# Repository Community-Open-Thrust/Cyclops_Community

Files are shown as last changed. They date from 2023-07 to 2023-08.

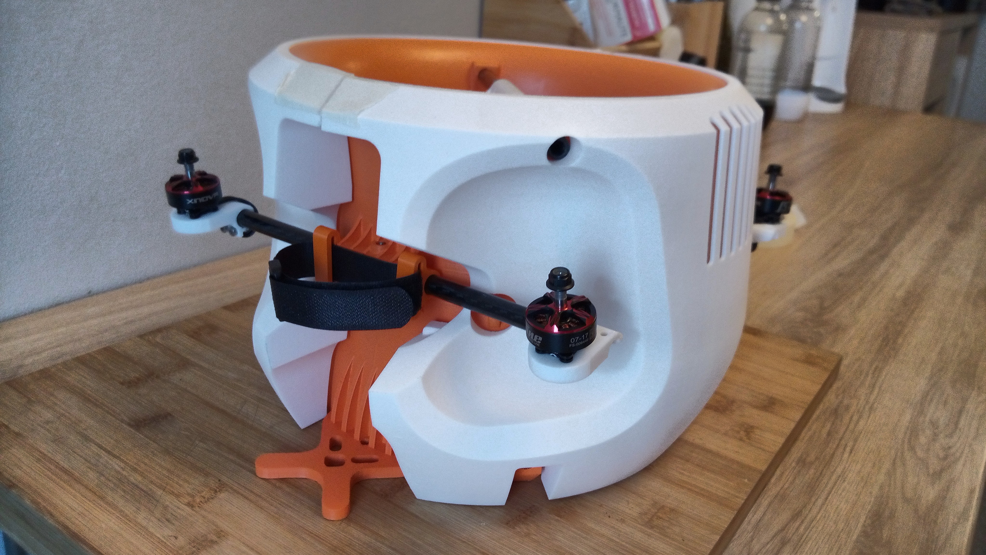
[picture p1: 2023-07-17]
Engineering/Photos-Assemblage-MarkII/IMG_20211008_180041_DRO.jpg

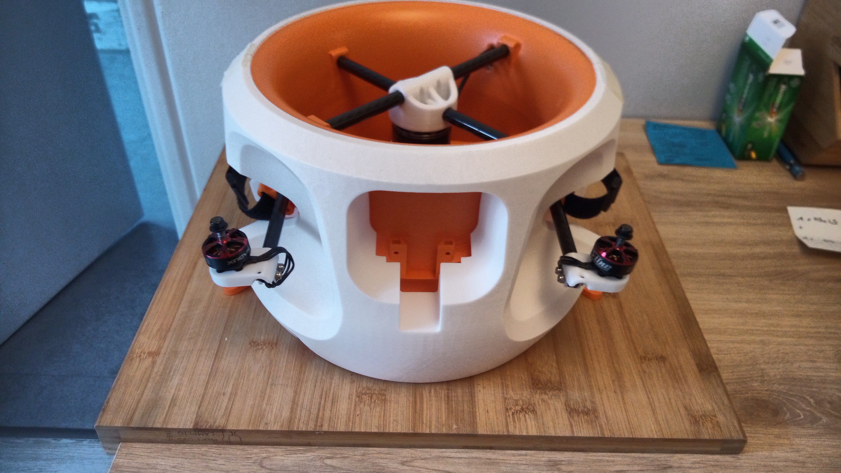
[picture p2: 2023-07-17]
Engineering/Photos-Assemblage-MarkII/IMG_20211008_180009_DRO.jpg

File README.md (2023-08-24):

# Cyclops / Cyclope Indoor Drone Community Edition

This is the repository for the Community Edition Release of the community of makers from Neva Aerospace Ltd (UK) for the turbo-drone Cyclope / Cyclops series for Indoor.

Cyclope v2 modifie - mise en situation interieur usine 2

Cyclops series are derived from Athena electric turbines / Electric Ducted Fans (EDF) 

# THE LICENCE IS CERN-OHL-S (Strongly Reciprocal) V2
https://ohwr.org/cern_ohl_s_v2.pdf


The LICENCE IS CERN Open Hardware Licence V2 "CERN-OHL-S V2" (Strongly Reciprocal). It applies to this repositrory and all Open-Thurst Community Repositories and contained sources.

Any further fork and/or modification must bear the following "Acknowledgement Notice" as per chapter 1.10 of Definition of the CERN-OHL-S V2 Licence:
"Acknowledgement of the Original Authors: Neva-Aero and the Human Team Members between 2016 and 2022 : F.M. Robert Vergnes, Valentin Bertrand, Kevin Pantoja, Olivier Chevillard, Elie de Fonclare, David Brotherton-Ratcliffe, Renaud-Pierre Blanpain, Anthony Gambus", and "Cyclops Series - Open-Thrust Community Edition - Licence CERN-OHL-S-V2", both Notice to be visible in the documentation with a link to the github Source.

And as per chapter 4 , the Visible Notice is "Cyclops Series - Open-Thrust Community Edition - Licence CERN-OSL-S-V2" and must be visible on the product.

# About using this repository
MAIN WILL NOT CHANGE.
The main of repository will be locked to the initial commit to avoid losing information. 
Please do create a new branch for a new version or create your own fork.
Please check the branch for the early or the last version of the project.

# Serialisation & History
The current Cyclops-K-Mark-II.2, it is an evolution of several design trials.
The first flight occured in May 2021 and then the prototyping went through several iterations.
The Cyclope-K-Mark-II has limitations and it requires more development to achieve its full potential.

# Warranties & Disclaimers

The Warranties and Disclaimers from the LICENCE IS CERN-OHL-S (Strongly Reciprocal) V2 apply to all Open-Thurst Community Repositories and contained sources.
https://ohwr.org/cern_ohl_s_v2.pdf

Extract:

6 DISCLAIMER AND LIABILITY 

6.1 DISCLAIMER OF WARRANTY – The Covered Source and any Products are provided ‘as is’ and any express or implied warranties, including, but not limited to, implied warranties of merchantability, of satisfactory quality, non-infringement of third party rights, and ﬁtness for a particular purpose or use are disclaimed in respect of any Source or Product to the maximum extent permitted by law. The Licensor makes no representation that any Source or Product does not or will not infringe any patent, copyright, trade secret or other proprietary right. The entire risk as to the use, quality, and performance of any Source or Product shall be with You and not the Licensor. This disclaimer of warranty is an essential part of this Licence and a condition for the grant of any rights granted under this Licence. 

6.2 EXCLUSION AND LIMITATION OF LIABILITY – The Licensor shall, to the maximum extent permitted by law, have no liability for direct, indirect, special, incidental, consequential, exemplary, punitive or other damages of any character including, without limitation, procurement of substitute goods or services, loss of use, data or proﬁts, or business interruption, however caused and on any theory of contract, warranty, tort (including negligence), product liability or otherwise, arising in any way in relation to the Covered Source, modiﬁed Covered Source and/or the Making or Conveyance of a Product, even if advised of the possibility of such damages, and You shall hold the Licensor(s) free and harmless from any liability, costs, damages, fees and expenses, including claims by third parties, in relation to such use. 

One last reminder, drones and/or turbines (electric ducted fans) can be dangerous if misused or made or used by non-trained technicians or engineers. You have been warned. All risks are yours.

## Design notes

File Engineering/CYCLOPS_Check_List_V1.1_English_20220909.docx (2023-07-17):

# CYCLOPS - TurboDrone

# PILOT CHECKLIST

# 1 PRE-FLIGHT

Purpose: To ensure that the aircraft is in flight order

## 1.1 Step 1: Central Turbine Inspection

• All the blades are present

• Rotors spin freely

• No major impact in the Shroud

## 1.2 Step 2: Inspection of auxiliaries

• All propellers are in good condition

• The motors do not rotate around the carbon axis

• The fairings are fixed and in good condition

## 1.3 Step 3: General Inspection

• No bare cables

• No free cables that could change when entering

• Landing feet are attached and in good condition

- Ensure that your HEREFLOW sensor is cable-connected and screwed to the drone
- Ensure that your Lidar sensor is cable-connected and screwed

# 2 PAYLOAD MOUNTING

Objective: Prepare the drone for an inspection mission

BEWARE THE DRONE CYCLOPS SERIES MUST HAVE A PAYLOAD TO FLY OR DEAD-WEIGHT MASS

## 2.1 Step 1: Choose your flight configuration

• Setup 1: Insta360 Camera

• Config 2: Feyiu Gimbal + Thermal Camera

• Config training: Add the fake camera (equivalent to Config1) with weight inside (orange fake camera)

## 2.2 Step 2: Mount the payload

• Mount the inspection elements on the front plate (camera, etc.)

• Mount balancing weights if needed

• Check balance - that the weights are correct for the chosen Config. – handle the drone by the top handle either by hand or through a carbon rod to check if there is any major disbalance.

Important: Make sure everything is secure and nothing can come loose in flight

# 3 GETTING STARTED

Objective: Prepare the drone for start-up

## 3.1 Step 1: Prepare the batteries

• Check the state of charge of the batteries

• Position the 2 batteries on the battery supports

• Fasten the batteries with the straps – make sure to lock the cables in the strap

• Mount low battery alarms on balancing sockets

• Make sure that no cables are close to the auxiliary motors

## 3.2 Step 2: Preparation of pilot equipment

• Switch on the Radio Control

• Turn on telemetry items

## 3.3 Step 3: Getting Started

• Connect the 2 batteries

• Check the connection between the drone and the RC (green led on the receiver and crossfire)

• Check the telemetry connection

• Check that the Pixhawk has initialized correctly (sound signal)

- Check that your RC respond on all modes: Stabilize, AltHold, Loitter – check on the telemetry screen
- Arm check: when armed on stabilize or althold ONLY the auxiliaries motors will start.

# 4 BEFORE THE FIRST TAKE OFF OF THE DAY

AFTER major transportation (airplane, trucks, or mishandling, or boat shipping) or several month unattended: Ground-run-up is mandatory

- Drone attached / strapped on a support of more than 5 KG – strap through the lower in-turbine carbon tube.
- Do not strap landing gears – strap on carbon tubes!
- Getting started & verification of use
- Power up in 10% increments for 10 seconds
- At each level check the noise (no abnormal vibration)
- Go to the next level +10% and thus up to 100% power

In the event of abnormal vibration at a bearing, stop the turbine and carry out the usual checks or suspend the activity.

• Once process is ended, cut the throttle. Do a quick visual inspection

• Add 5% throttle for 20-30s to cool motors of the EDF (central turbine).

# 5 LIFT-OFF

## 5.1 Step 1: Arm the drone

• Arm the drone (radio control)

Select mode: Stabilise or AltHOLD for take-off

It is advised not to take-off on Loitter indoor due to the nature of thr dround which may or may not be suitable for the Loitter sensor (Hereflow).

• Check that the 4 auxiliary motors are running well

• Very slightly increase throttle

• Check that the central turbine turns well

- In AltHold (and Loitter) take-off : the Central turbine ramps-up according to Pixhawk and it takes few seconds for Piwhaxk to ramps up the turbine – be gentle and patient.

## 5.2 Step 2: Put the drone in the air

• Gradually increase the throttle until the drone starts to lift (throttle approx. 50%) – be patient as turbine ramps for take-off is managed by Pixhawk.

• Give a small pulse on the throttle to put the drone in the air

• Stabilize the drone at eye level then start the mission

On K-001 & K002 drone on Stabilize and AltHold the drone needs a bit of pitch-forward as it tends to shift back – it is a known issue to be corrected. – Pixhawk does correct as soon as you switch to loiter mode.

## 5.3 Loiter mode:

When on Stabilize or AltHold and the drone is at +1M and stable:

- You can switch to Loiter,
- wait 2 seconds and move your drone gently around
- check if there is no “HERFLOW / XY error” – as this would indicate that the ground is not compatible with the ToF Herflow Senor sensor and you need to revert back to AltHold. If there is no error, you are free to loiter to your will.
- Fly Safe and respect regulations

# 6 LANDING

• Landing Modes: Stabilise, ALtHold, Loitter. All modes are fine for landing

The Landing gears can break on hard landing. Landing gears are wearables and are designed to break on hard landing to absorb the energy of a hard landing and keep the drone safe. You have spare landing gears and the landing gears can be changed easily with zip-tights.

- As soon as the pilot hears the battery alarm, he must IMMEDIATELY enter the landing phase
- You can set battery alarm on your RC or Telemetry (by default Alarm is set to Telemetry).

• Gradually reduce throttle to lose altitude

• A few centimetres from the ground (10-20cm), level off, then reduce the throttle again to land

Note: In this phase the drone is subject to ground effects corrected by Pixhawk on Loiter mode only. For Stabilize and AltHold pilot need to pay attention to landing phase.

• Once on the ground, cut the throttle. Do a quick visual inspection

• Add 5% throttle for 20-30s to cool motors for the central turbine. This is needed. Please avoid stopping the motor of the Cyclops abruptly. Abruptly stopping turbine motors creates a thermal discharge due to the high current within the motor and ESC.

Important: No battery failsafe is set - only the pilot is responsible for his battery level

Neva Aerospace / © - 2022 1 / 2

CYCLOPS CHECKLIST – Nr. 202209

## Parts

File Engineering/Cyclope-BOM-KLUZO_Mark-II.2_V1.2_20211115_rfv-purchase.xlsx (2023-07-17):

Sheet: Header
File: | Cyclope K BOM File
Version | 1.2
Date | 2021-01-19

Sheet: KLUZO_BOM_PROTO
Cyclope Kluzo BOM
Last Edited by |  |  | NEVA VB – 19/01/2021
0 – General Specifications
Reserved for Neva
MTOW (gr) |  | 3400
Available Payload (gr) |  | 631
Autonomy (min) |  | 11
1 – Ready-to-fly Kluzo (without inspection equipment)
Reserved for Neva
Item Name | Units | Makes | Details | Total Weight (gr)
I – Main Body
SHO | 2 | NEVA |  | 750
STA | 2 | NEVA
ROT | 2 | NEVA
BLA | 10 | NEVA
CAP | 2 | NEVA
AUX_SHO | 4 | NEVA |  | 100
AUX_STA | 2 | NEVA | Carbon tube + motor adapter | 20
AUX_BLA | 4 | HQPROP | HQ 3x4x3 V1S | 8
II – Electronics
MOT | 2 | TMOTOR |  | 275
ESC | 2 | CASTLE |  | 40
AUX_MOT | 4 | TMOTOR | TMOTOR F1507 kv2700 | 60
AUX_ESC | 1 | TMOTOR | ESC Tmotor 4in1 V45A 6s 32 BIT | 20
III – Flight Control
PIX_MINI 4 | 1 | HOLYBRO |  | 16
SONARS | 3 | MAXBOTIXS |  | 25
RC_CONTOL | 1 | TBS | 868 MHz crossfire RX (https://www.studiosport.fr/recepteur-tbs-crossfire-nano-rx-se-a16057.html) | 5
TELEM | 1 | TBD | 433MHz telemetry | 30
IV – Power System
BAT | 2 | SLS | For 11min Flight : SLS4500mAh 6S 30/60C | 1300
BEC | 1 | CASTLE | Castle 6S – 5v – 10a (1xfor Pixhawk, 1xfor Accessories) | 15
HARNESS | 1 | NEVA | Power harness : 16awg+ xt90 connectors | 80
PWR_MODULE | 1 | TBD | Power module for pixhawk | 25
 |  |  | Total RTF weight (gr) | 2769
2 – Inspection Equipment
To be completed by Pilgrim
Item Name | Units | Makes | Details (please provide internet links) | Total Weight (gr) | Remaining Payload (gr)
Equipement de Base
Led lights | 4 | E44 electronique | 1W led light cold white(6000K) 3-3,6V (1Gr/led) http://www.e44.com/composants/composants-actifs/optoelectronique/led/leds-cms/led-haute-puissance-1w-blanc-froid-LED1WCMS-BLANC.html | 4 | 558.2 | ATTENTION : Température max : 125°C – Polycarbonate en impression obligatoire – Mettre les radiateurs dans le flux des moteurs aux
Heat dissipator led lights | 4 | RS component | https://fr.rs-online.com/web/p/dissipateurs-de-chaleur/7226827/?matchtype=&pla-303373399821&gclsrc=aw.ds | 40
FPV camera | 1 | Foxeer | 1 foxeer t-rex micro 1500tvl camera used for navigation https://www.foxeer.com/foxeer-t-rex-micro-1500tvl-6ms-latency-super-wdr-fpv-camera-g-308 | 8.6
FPV transmitter | 1 | TBS | Pro32Hv 25-1000mW 5,8Ghz https://www.studiosport.fr/emetteur-video-unify-pro32-hv-mmcx-team-black-sheep/ | 8.7
FPV Antenna | 1 | Foxeer | Foxeer pagoda Pro RPSMA RHCP | 11.5
Config 1 : camera 360°
SUPPORT CAMERA | 1 | Neva | NEW CAP INLET avec support camera | 50 | 378.2
360° camera | 1 | Insta360 | Camera Insta ONE R | 130 |  | DIMENSIONS : long 72 x hauteur 48 x profondeur 43
Config 2 : camera thermique
Gimbal/Stabilisateur Feiyu WG2 | 1 | FEIYUTECH | https://www.feiyu-tech.com/wg2/ | 238 | 210.2
FLIR Vue Pro | 1 | FLIR | https://www.flir.fr/products/vue-pro/ | 110

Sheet: Purchase_Parts-Suppliers
 | Item | Unit for 1 drone | Link 1 (FR) | Price total (€) unitaire | Prix Total | Link 2 (China) | Price (€) | Link 3 (USA) | Price (€)
Semaine 1 | Pixhawk Mini 4 Holybro | 1 | https://www.studiosport.fr/controleur-pixhawk-4-mini-holybro-a16951.html | 179.00 € | 179.00 €
 | Carrier Board Pixhak | 1 | https://www.airbot-systems.com/produit/mini-carrier-board-pdb-combo-pixhawk-cube/?lang=en | 100.00 € | 100.00 € | https://hexadrone.fr/cube-carrier-board/1753-mini-carrier-board-pour-pixhawk-2-hex-0094393522485.html
 | Pixhawk 2.1 | 1 | https://www.airbot-systems.com/produit/cube-orange-pixhawk2-1/?lang=en | 250.00 € | 250.00 € | https://www.robotshop.com/eu/en/cubepilot-the-cube-orange-standard-set-ads-b-carrier-board.html
 | HQ 3x4x3 lot de 4 | 3 pack of 4 | https://www.banggood.com/fr/HQProp-DP3X4X3-3-blade-3Inch-Poly-Carbonate-POPO-Propeller-2CW+2CCW-p-1530875.html?ID=6157193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 |  |  | https://fr.banggood.com/HQProp-DP3X4X3-3-blade-3Inch-Poly-Carbonate-POPO-Propeller-2CW+2CCW-p-1530875.html?ID=6157216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 | 9.00 € | BAD SERIES BURNING
 | T-motor f1507 kv 2700 | 4 | https://www.drone-fpv-racer.com/t-motor-f1507-2700kv-5494.html | 19.00 € | 76.00 € | https://fr.banggood.com/T-Motor-F1507-1507-2700KV-3-6S-or-3800KV-3-4S-Brushless-Motor-for-Cinewhoop-RC-Drone-FPV-Racing-p-1582951.html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 | 66.00 € | BAD SERIES BURNING
 | MOTEURS X-NOVA SMOOTH LINE 2207 - 1700KV | 4 | Moteur : https://www.drone-fpv-racer.com/moteurs-x-nova-smooth-line-2207-boite-de-4-4739.html | 22.00 € | 88.00 € |  |  | Martk-II.2
 | GEMFAN 4032 WINDANCER - 4PCS | 4 | https://www.drone-fpv-racer.com/gemfan-4032-windancer-4pcs-4886.html#/1137-couleur-clear_red | 3.00 € | 12.00 € |  |  | Mark-II.2
 | XT90 anti-spark | 3 | https://www.amazon.fr/Lead-Tech-Anti-%C3%89tincelle-Connecteur-Adaptateur/dp/B07D6QH421 | 4.00 € | 12.00 € | https://fr.banggood.com/Amass-Anti-Spark-Sparkproof-Connector-Plug-XT90-S-For-Batttery-p-946409.html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 | 7.00 €
 | Bullet banana connector 3,5mm | 1 | pack | 6.00 € | 6.00 € | https://fr.banggood.com/20-Pairs-3_5mm-Gold-Bullet-Banana-Connector-Plug-Male-and-Female-For-ESC-Battery-Motor-p-934281.html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 | 6.00 €
 | T-Motor MN4010 KV475 | 2 | https://www.aerolab.de/brushless-motoren/t-motor-mn-serie/t-motor-mn4010-kv475_100012_1011 | 71.00 € | 142.00 € | https://store-en.tmotor.com/goods.php?id=342
Semaine 2 | ESC YGE 35LVT | 2 | http://www.helidigital.com/shop/controleurs-/3958-yge-35-lvt.html | 120.00 € | 240.00 € | https://www.hoelleinshop.com/e-vendo.php?shop=hoellein&SessionId=&a=search&SearchStr=YGE+35LVT
 | BEC 6S Matek | 1 | https://www.drone-fpv-racer.com/matek-micro-bec-630v-5v9v-6646.html?search_query=bec&results=175 | 7.90 € | 7.90 €
 | TMOTOR ESC 4in1 45A VELOX V2 | 1 | https://www.drone-fpv-racer.com/t-motor-velox-v45a-v2-4in1-esc-6235.html | 41.90 € | 41.90 €
 | Radio Taranis X9 Lite | 1 | https://www.studiosport.fr/radio-taranis-x9-lite-a18054.html | 107.00 € | 107.00 €
 | 18650 Accu | 2 | https://www.studiosport.fr/batterie-18650-3000mah-sony-a19219.html | 13.00 € | 26.00 €
 | External Baro - Adafruit BMP280 | 1 | https://www.gotronic.fr/art-capteur-de-t-et-de-pression-ada2651-23891.htm | 15.00 € | 15.00 €
 | KIT Crossfire TBS | 1 pack only (do not multiply by the number pf drones) | https://www.drone-fpv-racer.com/tbs-crossfire-micro-tx-v2-starter-set-3585.html | 139.90 € | 139.90 € | https://www.studiosport.fr/crossfire-nano-tx-starter-set-tbs-a20613.html |  | https://www.drone-fpv-racer.com/tbs-crossfire-nano-tx-6687.html
 |  |  |  |  |  | *
Semaine 3 | Camera 360 – Insta One R Twin edition | 1 | https://www.studiosport.fr/insta360-one-r-twin-edition-a19552.html | 509.00 € | 509.00 €
 | Telem 433 | 1 | https://www.studiosport.fr/kit-de-telemetrie-mini-433mhz-100mw-3drobotics-a19366.html | 29.9 | 29.9 | https://www.studiosport.fr/kit-telemetrie-fpv-radio-433mhz-v3-a16473.html | En attente confirmation Valentin
 | FPV Transmitter | 1 | https://www.studiosport.fr/emetteur-video-unify-pro32-hv-mmcx-team-black-sheep/ | 49.9 | 49.9 | https://www.fpv-fly.fr/tbs-unify-pro32-hv-mmcx.html
 | Antenna | 1 | https://www.studiosport.fr/antenne-singularity-5-8-sma-coudee-a-90-long-rhcp-truerc-a19037.html | 21.9 | 21.9
Semaine 4 | Lipo SLS 6S 4500mAh | 2 | https://www.stefansliposhop.de/en/batteries/sls-quantum/sls-quantum-30c/sls-quantum-4500mah-6s1p-22-2v-30c-60c::1684.html | 86.00 € | 172.00 € | https://www.stefansliposhop.de/en/information-for-retailers-business-consumers:_:1030.html
 | Lidat Lite Down range | 1 | https://www.robotshop.com/eu/fr/capteur-distance-laser-lidar-lite-3.html | 130.00 € | 130.00 €
 | Sonar maxbotix EZ4 I2C -MB1242 | 3 | https://www.robotshop.com/eu/fr/sonar-performance-i2cxl-maxsonar-ez4-maxbotix.html | 40.00 € | 120.00 €
 | Sonar maxBotix EZ0 | 3 | https://www.robotshop.com/eu/fr/capteur-ultrason-ez0-maxbotix.html | 27.00 € | 81.00 € | Note : 1 facing front (to protect camera) + 1 facing back (to protect eectronics) + 1 facing down (for smooth landing) |  | https://www.gotronic.fr/art-lv-maxsonar-ez0-11547.htm
 | LED éclairage (300Lumen) | 4 | https://www.amazon.fr/gp/product/B08QCLL21S/ref=ppx_yo_dt_b_search_asin_image?ie=UTF8&th=1 | 3 | 12 |  |  | https://www.e44.com/composants/composants-actifs/optoelectronique/led/leds-cms/led-haute-puissance-3w-blanc-froid-LED3WCMS-BLANC.html
 | LED Beamo (alternate) |  | https://www.amazon.fr/dp/B0849ZP618/ref=cm_sw_r_wa_apa_glt_i_KY1DYVP49E1CYM1X9PAC?th=1 | 70
 | Radiator for LED
 | Gimbal | 1 | https://www.amazon.fr/Feiyu-Tech-Stabilisateur-motoris%C3%A9-Smartphone-Action/dp/B071L93YDV | 245.9 | 245.9
 | Tubes carbones | 2 | https://www.carbonetube.net/produit.php?cat=TCUB | 13 | 26 | Tube carbone 10x7x1000mm DRAPAGE (REF0132CTPP1070-1)
 | SD Card V60 or SanDisk Pro | 1 | https://www.amazon.fr/dp/B0713QB6PB?psc=1&smid=A1X6FK5RDHNB96&ref_=chk_typ_imgToDp | 60 | 60 | Sandisk Pro extrem
 | RpiZero WH | 1 | https://www.kubii.fr/cartes-raspberry-pi/2076-raspberry-pi-zero-wh-kubii-3272496009394.html | 15 | 15 | https://www.amazon.fr/gp/product/B07C7FHJDX/ref=ppx_yo_dt_b_asin_image_o04_s00?ie=UTF8&psc=1
 | Battery Buzzer | 1 | https://www.amazon.fr/gp/product/B07Q9JQ2ZZ/ref=ppx_yo_dt_b_asin_title_o01_s00?ie=UTF8&psc=1 | 13 | 13
 | I2C Hub 6 | 2 | https://www.gotronic.fr/art-hub-6-ports-i2c-grove-103020272-31348.htm | 2 | 4
 | I2C Hib x8 | 1 | https://www.amazon.fr/gp/product/B08CXWVSMC/ref=ppx_yo_dt_b_asin_title_o00_s00?ie=UTF8&psc=1 | 11 | 11
 | Grive Cable Y | 1 | https://www.gotronic.fr/art-5-cables-grove-en-y-110990092-30772.htm | 5 | 5
 | I2C Hib x4 PXWH | 1 | https://www.amazon.fr/gp/product/B08212X27Q/ref=ppx_yo_dt_b_asin_title_o01_s00?ie=UTF8&psc=1 | 9 | 9
 | I2C HAT - SparkFun Qwiic HAT | 1 | https://www.amazon.fr/gp/product/B07JBK2LBZ/ref=sw_img_1?smid=&psc=1 | 12 | 12 | https://www.sparkfun.com/products/14459
 | RTK Module I2C male | 1 | https://www.amazon.fr/dp/B076GP5B94?psc=1&smid=A1X7QLRQH87QA3&ref_=chk_typ_imgToDp | 5 | 5 | DS3231
 | Radiator RpiZerp | 1 | https://www.amazon.fr/Aluminium-Dissipateur-Radiateur-Raspberry-Pi%C3%A8ces/dp/B01LXWK626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 | 3 | 3
 | RTK Module - Female | 1 | https://www.amazon.fr/gp/product/B07MB8YGCR/ref=ppx_yo_dt_b_asin_title_o01_s00?ie=UTF8&psc=1 | 18 | 18 | DS3231 // R&D only | TBC
 | Thoman manhole case | 1 | https://www.thomann.de/fr/hardcase_hn16b_bass_drum_case.htm | 150 | 150
 | Mousse Ptédécoupée | 5 | https://www.vexi.fr/details/valises-plastique/mousses-valises/mousse-predecoupee-620mm/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 | 30 | 150 | https://www.amazon.fr/HMF-pr%C3%A9d%C3%A9coup%C3%A9e-Personnalisable-Mallette-Tabletop/dp/B07GTP3S97
 | Mousse Laser découpe JPJ | 1 | https://www.jpj-mousse.fr/ | 500 | 500
 | Carénages Extérieur | 2 | Sculpteo | 380 | 760
 | Shroud Intérieur | 1 | pm@freelabster.com | 700 | 700 | info@invent3d.design
 | Vernis
 | Bande Reflec | 1 | https://www.amazon.fr/gp/product/B0814VMWV6/ref=ppx_yo_dt_b_asin_title_o00_s00?ie=UTF8&psc=1 | 11 | 11
 | Autocollant Reflec | 1 | https://www.amazon.fr/gp/product/B00EXQQFEW/ref=ppx_yo_dt_b_asin_title_o00_s00?ie=UTF8&psc=1 | 6 | 6
 | 41

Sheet: ShortSpecs
Short Parts List
Item | Unit for 1 drone
Controlller & Power:
Carrier Board Pixhak | 1
Pixhawk 2.1 | 1
MOTEURS X-NOVA SMOOTH LINE 2207 - 1700KV | 4
GEMFAN 4032 WINDANCER | 4
ESC Auxiliaire - F35 - Heli T-MOTOR | 4
EDG Athena: (Central Booster)
T-Motor MN4010 KV475 | 2
Lipo SLS 6S 4500mAh | 2
Radio:
Radio Taranis X9 Lite | 1
KIT Crossfire TBS | 1
Telem 433 | 1
FPV Transmitter | 1
Antenna | 1
ASMV Module:
Sonar maxbotix EZ4 I2C | 3
RpiZero WH | 1
I2C HAT - SparkFun Qwiic HAT | 1
RTC Module I2C male | 1

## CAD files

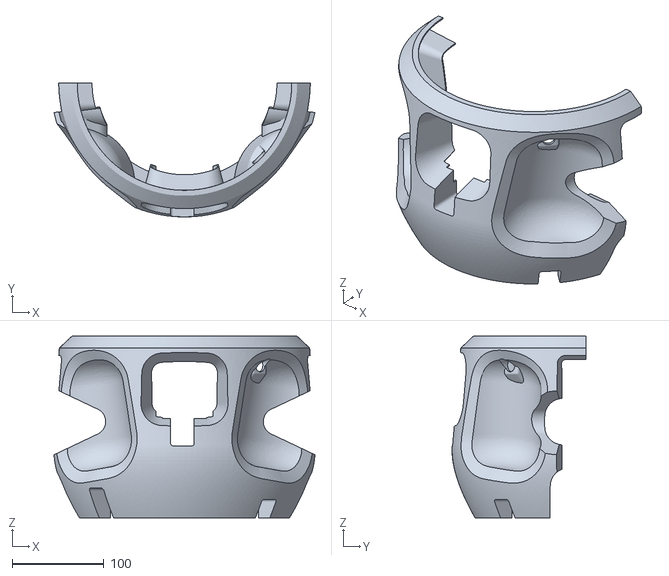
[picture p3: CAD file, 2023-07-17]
Engineering/CAD_3D/Covers_Capotages/Front-carenage-cyclope-mkII.stl
285.0 x 146.2 x 198.5

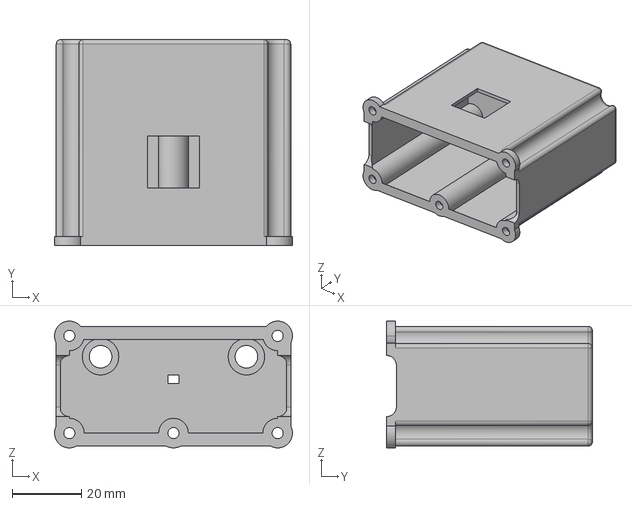
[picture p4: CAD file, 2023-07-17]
Engineering/CAD_3D/Platine-arriere-PIXHAWK-MKII/Boite-radio-MKII.step
68.5 x 59.3 x 36.5 mm

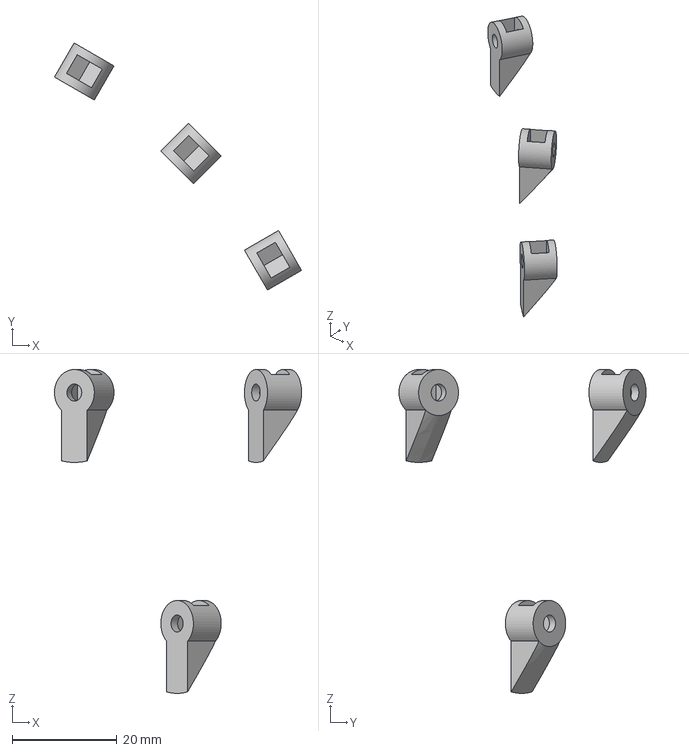
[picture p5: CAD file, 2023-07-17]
Engineering/CAD_3D/STEP/attache_pix.step
47.1 x 47.1 x 61.7 mm

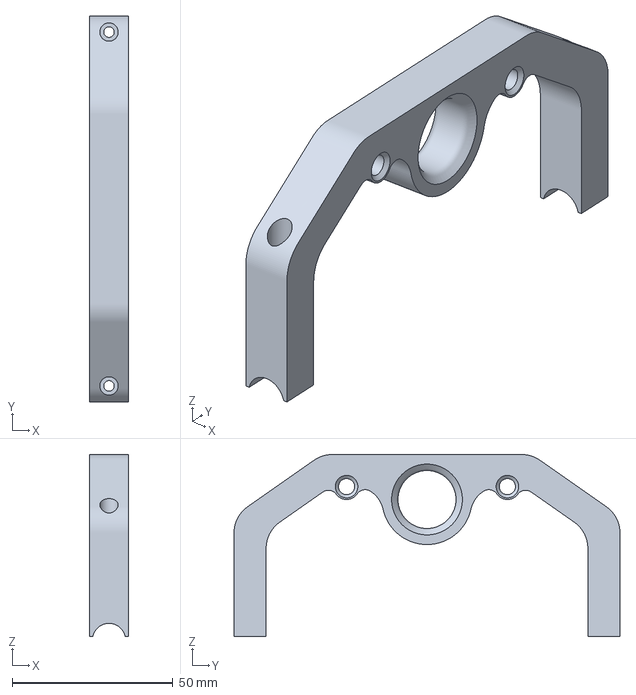
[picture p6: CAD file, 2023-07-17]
Engineering/CAD_3D/STL-AVRIL2021/NEVA-CYLCOPE-poignée-V2.amf
12.0 x 120.0 x 56.6 mm

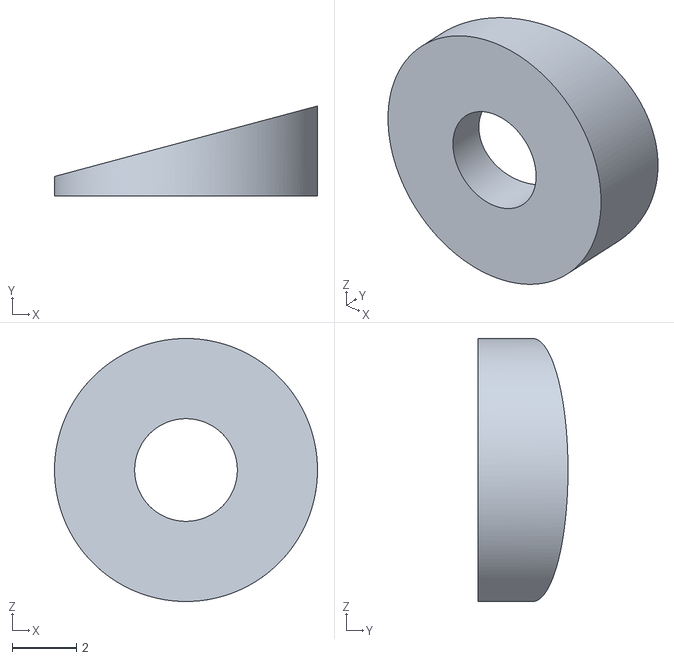
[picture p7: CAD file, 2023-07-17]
Engineering/CAD_3D/STL-AVRIL2021/Rondelle-pixhawk/rondelle2.stl
8.20 x 2.81 x 8.20

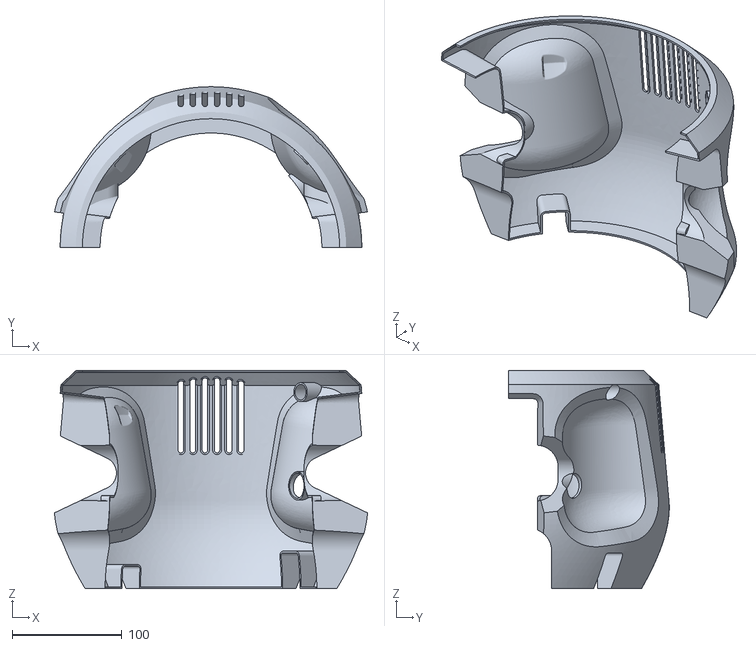
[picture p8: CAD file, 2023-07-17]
Engineering/CAD_3D/Covers_Capotages/Rear-carenage-cyclope-mkII.stl
285.0 x 146.2 x 198.5

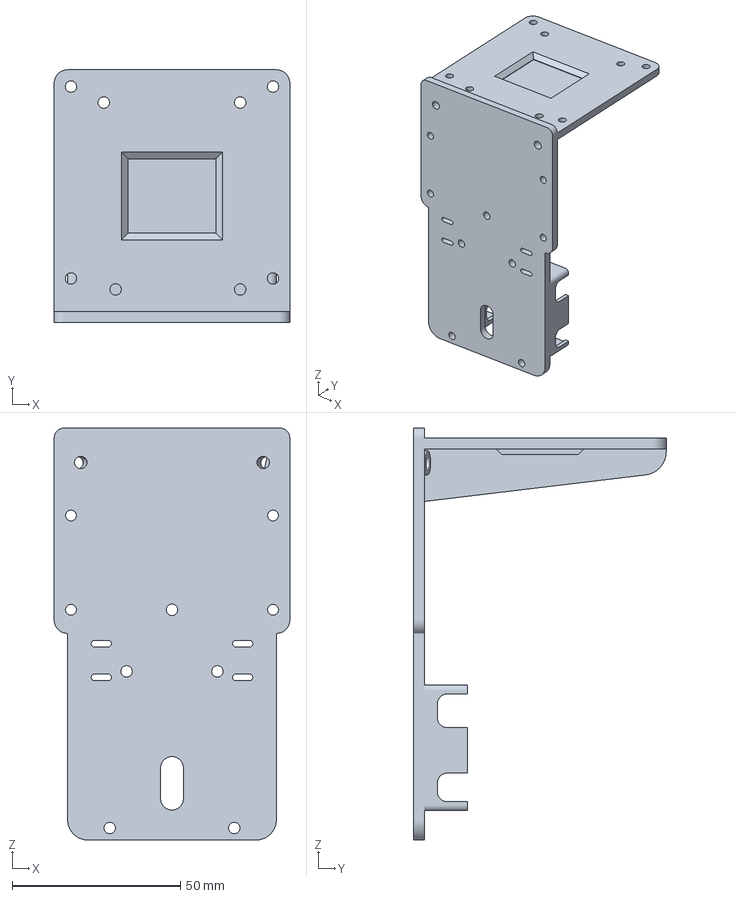
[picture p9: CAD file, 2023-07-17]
Engineering/CAD_3D/Platine-arriere-PIXHAWK-MKII/Grande-platine-ready.amf
70.0 x 75.0 x 122.4 mm

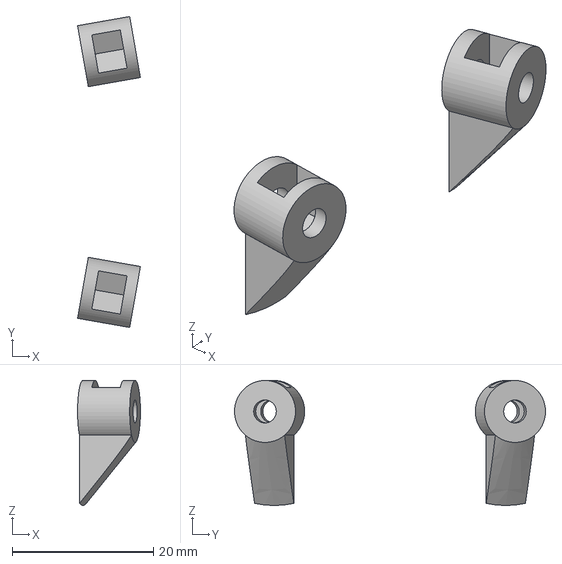
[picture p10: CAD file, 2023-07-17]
Engineering/CAD_3D/STEP/attache-esc.step
8.91 x 44.1 x 17.7 mm

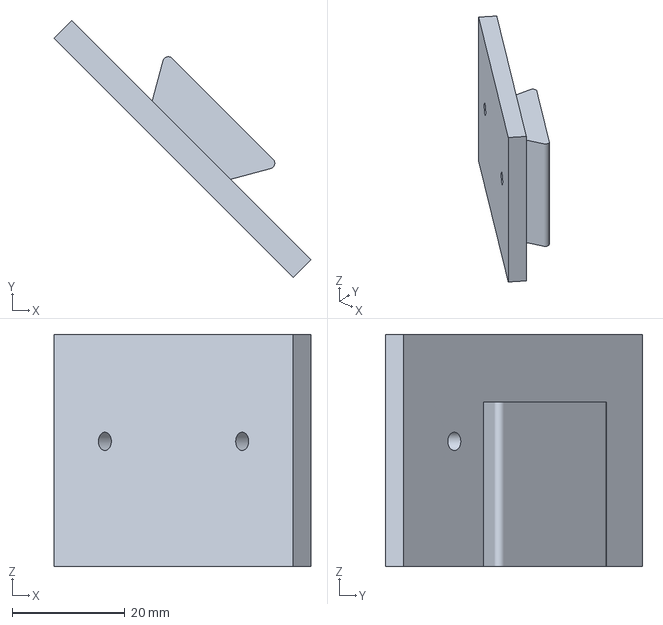
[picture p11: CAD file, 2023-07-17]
Engineering/CAD_3D/STL-AVRIL2021/NEVA-CYLCOPE-platine-tenon-salon.amf
45.6 x 45.6 x 41.2 mm

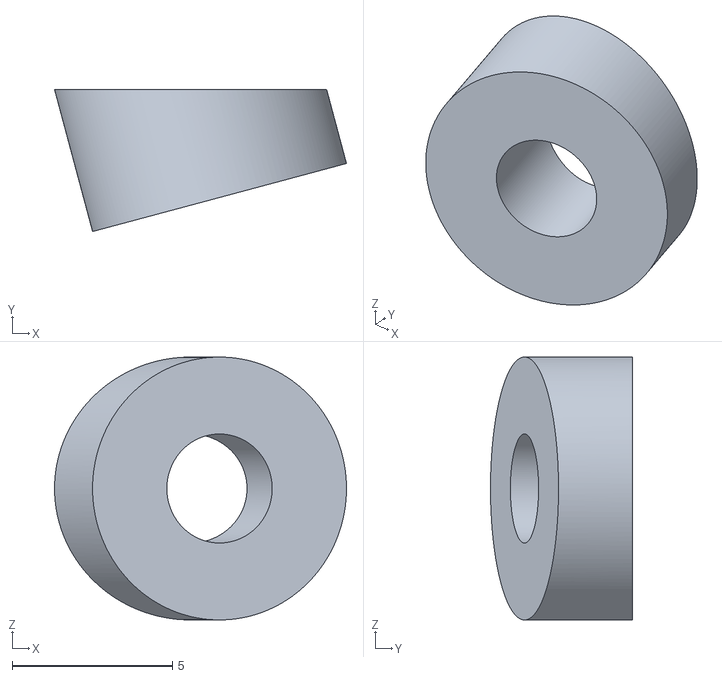
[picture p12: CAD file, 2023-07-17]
Engineering/CAD_3D/STL-AVRIL2021/Rondelle-pixhawk/rondelle1.stl
9.11 x 4.43 x 8.20

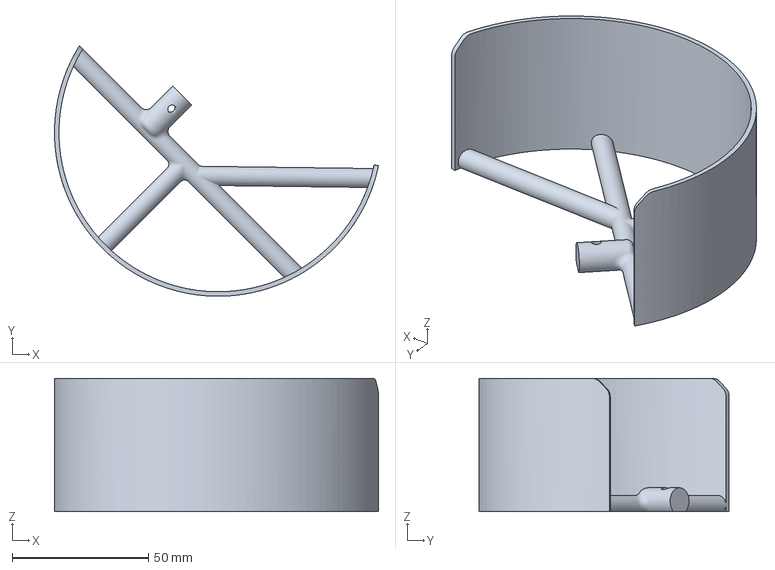
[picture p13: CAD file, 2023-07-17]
Engineering/CAD_3D/STL-AVRIL2021/CARENAGE-MARKII-0921.amf
119.1 x 92.1 x 49.0 mm

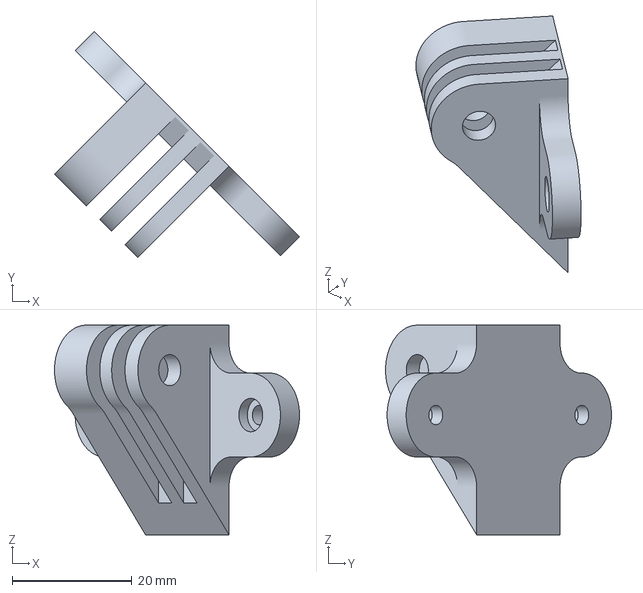
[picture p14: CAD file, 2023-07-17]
Engineering/CAD_3D/STL-AVRIL2021/NEVA-CYLCOPE-support-gopro.amf
40.9 x 37.7 x 35.0 mm

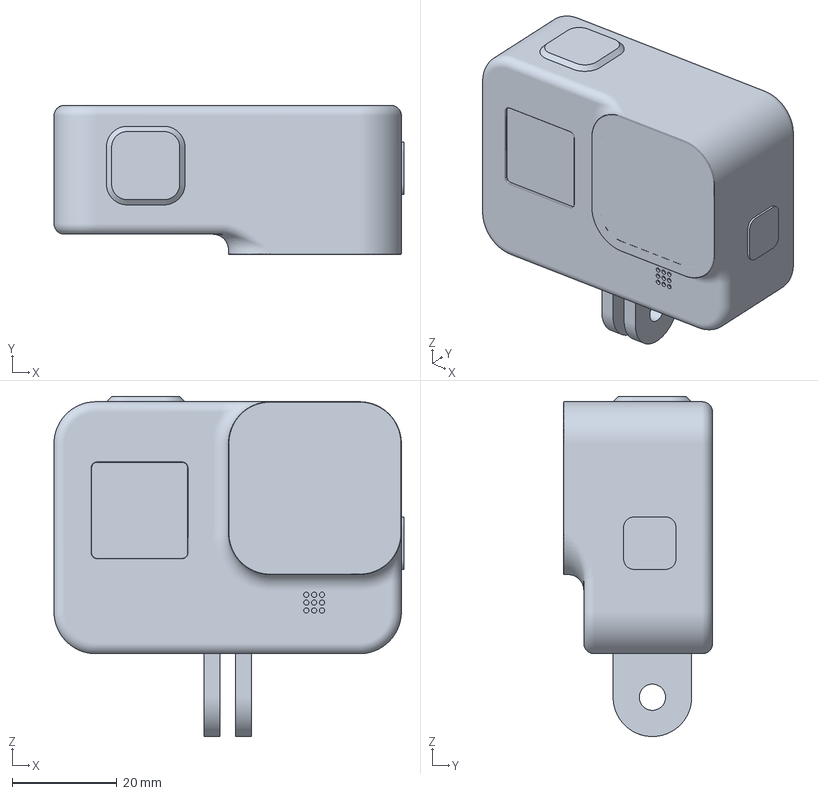
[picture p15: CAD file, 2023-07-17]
Engineering/CAD_3D/STL-AVRIL2021/Go-pro.amf
66.8 x 28.5 x 64.9 mm

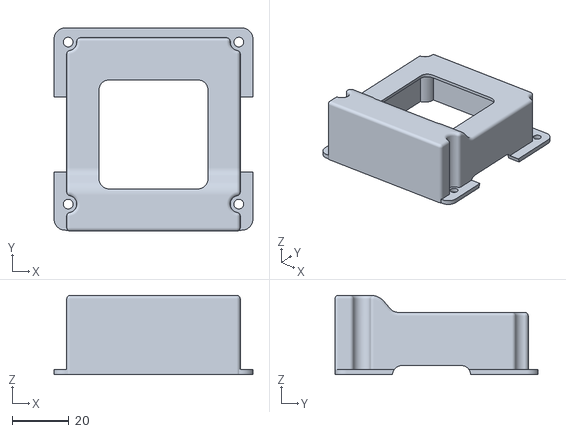
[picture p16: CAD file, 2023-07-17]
Engineering/CAD_3D/Platine-arriere-PIXHAWK-MKII/Boite-pixhawk.stl
70.0 x 71.5 x 27.9

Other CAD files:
Engineering/CAD_3D/Platine-arriere-PIXHAWK-MKII/Platine-arriere-MKII.step
Engineering/CAD_3D/Platine-arriere-PIXHAWK-MKII/Platine-arrière-MKII.stl
Engineering/CAD_3D/Platine-arriere-PIXHAWK-MKII/rondelle.amf
Engineering/CAD_3D/Platine-arriere-PIXHAWK-MKII/Fixation-pixhawk.FCStd
Engineering/CAD_3D/Platine-arriere-PIXHAWK-MKII/Boite-Radio-MKII.stl
Engineering/CAD_3D/Platine-arriere-PIXHAWK-MKII/Boite-Radio.amf
Engineering/CAD_3D/Platine-arriere-PIXHAWK-MKII/Boite-pixhawk-MKII.step
Engineering/CAD_3D/Platine-arriere-PIXHAWK-MKII/Protection-pixhawk.amf

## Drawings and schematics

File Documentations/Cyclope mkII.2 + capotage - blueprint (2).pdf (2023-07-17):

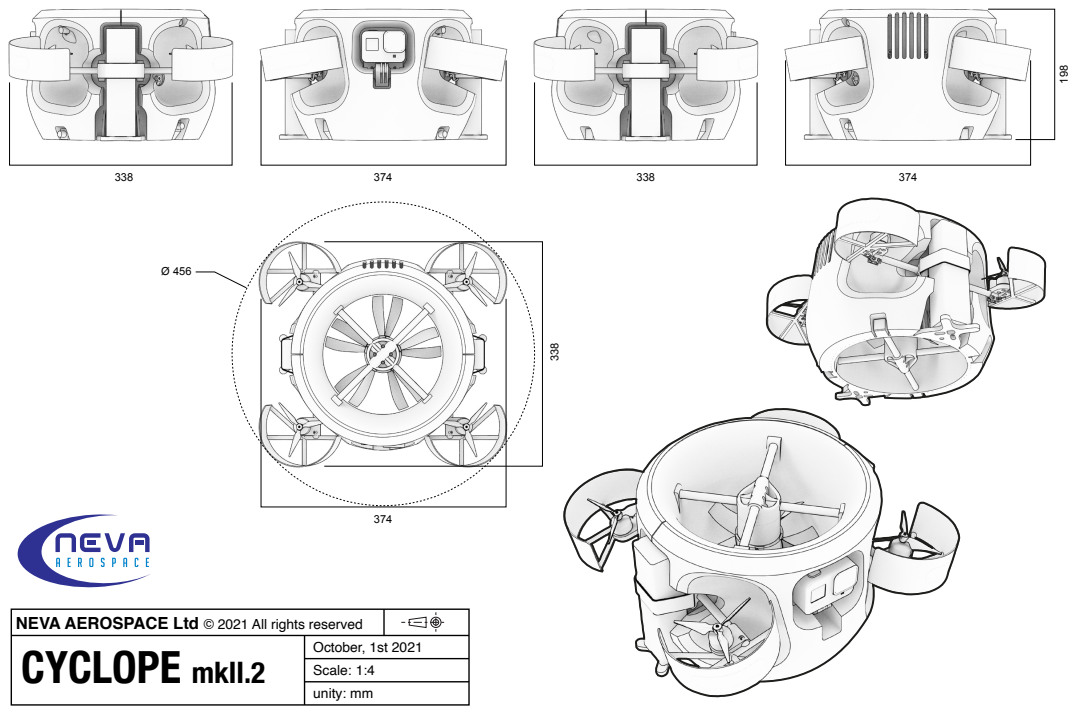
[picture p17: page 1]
Scale: 1:4 unity: mm

NEVA AEROSPACE Ltd © 2021 All rights reserved
CYCLOPE mkII.2 | October, 1st 2021

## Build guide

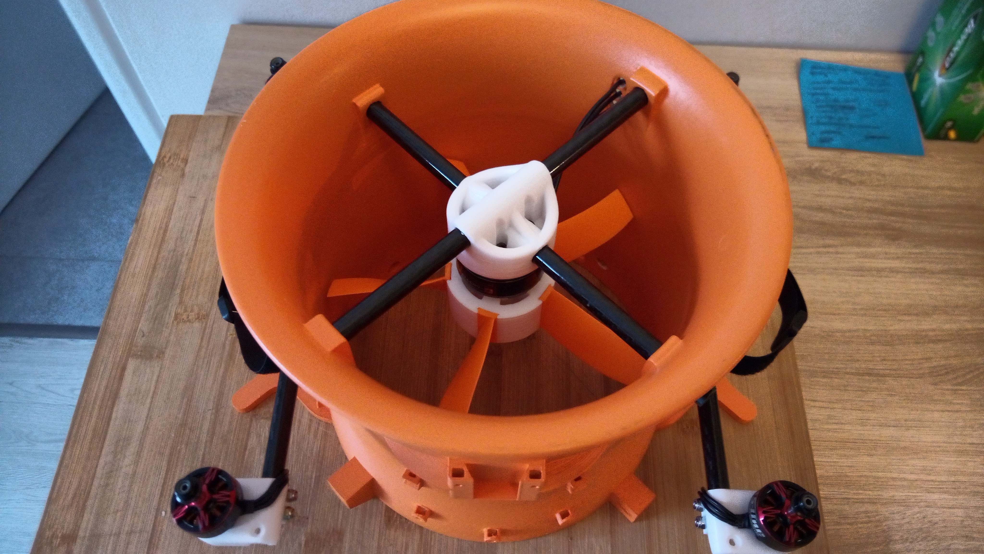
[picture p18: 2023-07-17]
Engineering/Photos-Assemblage-MarkII/IMG_20211008_175642_DRO.jpg

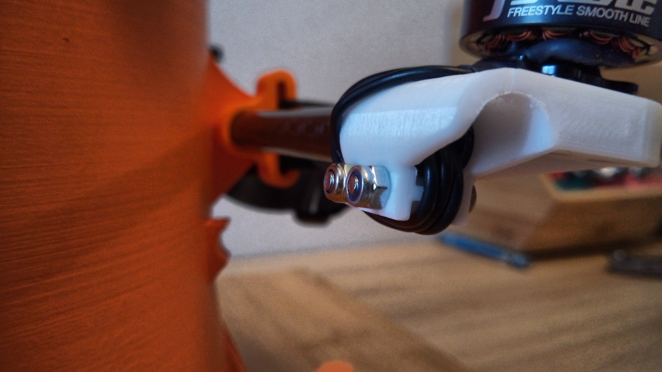
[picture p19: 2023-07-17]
Engineering/Photos-Assemblage-MarkII/IMG_20211008_175418_DRO.jpg

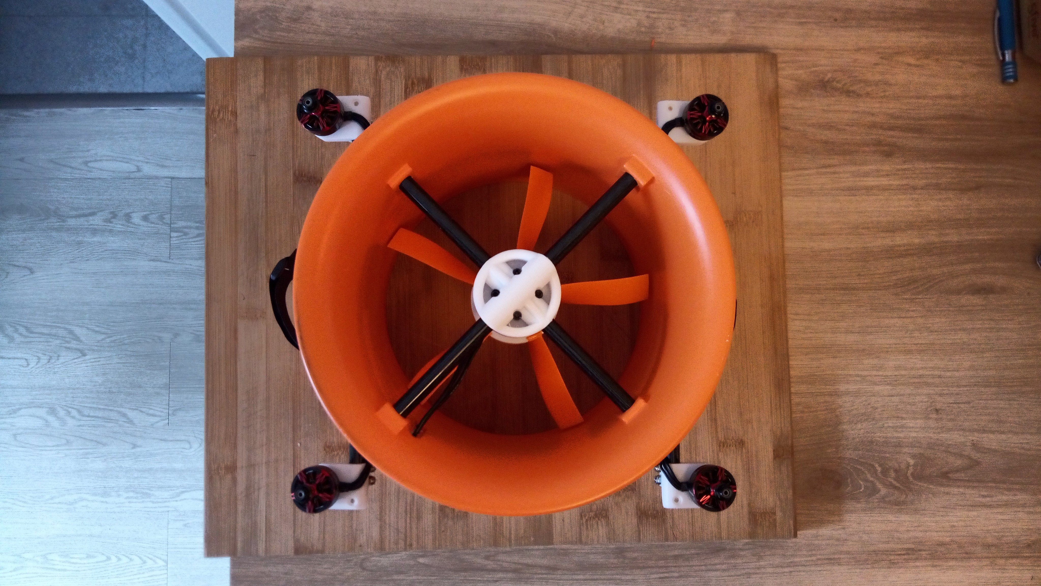
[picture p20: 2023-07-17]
Engineering/Photos-Assemblage-MarkII/IMG_20211008_175357_DRO.jpg

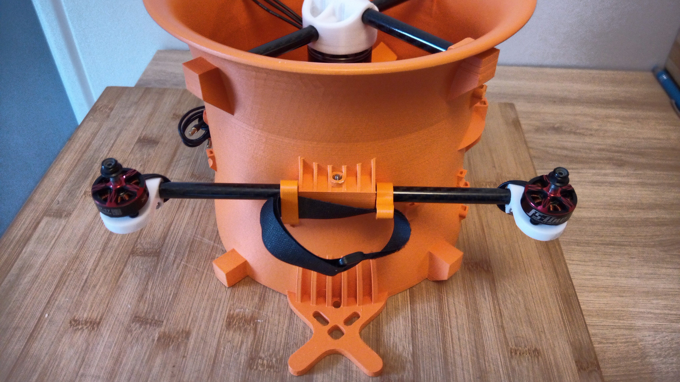
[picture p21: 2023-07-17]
Engineering/Photos-Assemblage-MarkII/IMG_20211008_175430_DRO.jpg
